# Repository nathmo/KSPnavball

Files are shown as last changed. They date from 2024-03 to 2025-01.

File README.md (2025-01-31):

# KSPnavball
This is a mechanical navball for a custom KSP gamepad



# Current state
currently it can be assembled but the wheel have nylon wheel and are too slippery. I'm experimenting with wheel made out of TPU but I need something even more rubbery and sticky. 
Regarding the software the main idea is here and the ball move but due to the slippage it's hard to tell if the code is doing it's job or if I fucked up the math to get the transform. (plus it definitely need some tunning)
anyways, feel free to build it and help me iron out the kink :)


# open issue
Ball slippage, omniwheel grip issue. I need to find a way to make the wheel more sticky and ruberry so that it works correctly.

# Hardware
|QTY|Name|Link|total price|
|---|----|----|----|
|25X|M3 5 mm depth 4.5mm diamater heat insert |https://www.aliexpress.com/item/1005003582355741.html|3.5$|
|25X|M3 screw | ||
|3X |omniwheel |https://www.aliexpress.com/item/32960657744.html| 8$|
|3X |DC motor |https://www.aliexpress.com/item/33022320164.html|  7$|
|2X |Hbridge DRV8833 |https://www.aliexpress.com/item/1005006444609771.html| 2.5$|
|1X |3 axis magnetometer ||  4.5$ |
|1X |magnet cylinder 10x2mm |https://www.aliexpress.com/item/1005006362930902.html| 2$ |
|1X |arduino nano |https://www.aliexpress.com/item/1005005702204423.html|2.5$|
Total = ~30 $ + 3D printed part + transparent window

one laser cutted sheet of 5mm transparent material is required. It should be engraved with the center sign of the navball.
the plastic part should not require any support and can be printed on a 15 x 15 [cm] bed
you will find the required file to print in the folder ToPrint, same for the folder toCut

# Wiring
need to document

# Software

https://kerbalsimpitrevamped-arduino.readthedocs.io/en/latest/payloadstructs.html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

https://kerbalsimpitrevamped-arduino.readthedocs.io/en/latest/payloadstructs.html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
https://www.instructables.com/KerbalController-a-Custom-Control-Panel-for-Rocket/

# Kinematic


The sphere is 90 mm in diameter
the wheel are 50 mm in diameter
the wheel are 120° apart (see from the top) and 45° raised from the horizontal plane

To compute the required motor commande $\alpha_1, \alpha_2, \alpha_3$ we need to break down the problem in two parts : 
1) finding the required rotation to go from the current navball orientation to the target one.
2) project this rotation on the wheels so that we know how much to rotate each motor.

### Find the required rotation
this is solved using [quaternion](https://en.wikipedia.org/wiki/Quaternion). We know two things :
1) the ball current orientation in the form of a unitary quaternion $(c_0, c_1, c_2, c_3)$ and
2) the target orientation in the form of a unitary quaternion $(t_0, t_1, t_2, t_3)$

from theses we know that there must exist a unitary quaternion such that $q \cdot c = t $ and thus we can deduce $q = tc^{-1}$
$c^{-1}$ being the conjugate of c, compute as $c^{-1}=(c_0, -c_1, -c_2, -c_3)$. unitary mean that the norm $c_0^2+c_1^2+c_2^2+c_3^2$ of the quaternion is equal to 1.
in practice this is compute like this :

$$
\begin{aligned}
q_0 &: c_0 t_0 + c_1 t_1 + c_2 t_2 + c_3 t_3, \\
q_1 &: -c_1 t_0 + c_0 t_1 - c_3 t_2 + c_2 t_3, \\
q_2 &: -c_2 t_0 + c_3 t_1 + c_0 t_2 - c_1 t_3, \\
q_3 &: -c_3 t_0 - c_2 t_1 + c_1 t_2 + c_0 t_3.
\end{aligned}
$$

$q_0$ represent the ammount of rotation and $q_1, q_2, q_3$ represent the rotation axis direction $(x,y,z)$

### project it on the motor axis
we use linear algebra to project the quaternion axis on the axis of each motor. then we scale this by the required rotation.

first we can precompute the vector basis on which we are going to project the rotation (3 vector that represent the rotation made by the three omniwheel)
we have our motor raised 45° from the horizontal plane. the unit axis for the first motor is thus :

$$
\text{First axis } (u_1): \text{Rotate vertical } (z) \ 45^\circ \text{ around } y:
u_1 = \begin{bmatrix}
\frac{\sqrt{2}}{2} \\
0 \\
\frac{\sqrt{2}}{2}
\end{bmatrix}.
$$

then we apply a $\pm 120°$ rotation around the z axis and obtain the two other vector.

$$
\text{Second axis } (u_2): \text{Rotate } u_1 \ +120^\circ \text{ around } z:
u_2 = \begin{bmatrix}
-\frac{\sqrt{2}}{4} \\
\frac{\sqrt{6}}{4} \\
\frac{\sqrt{2}}{2}
\end{bmatrix}.
$$

$$
\text{Third axis } (u_3): \text{Rotate } u_1 \ -120^\circ \text{ around } z:
u_3 = \begin{bmatrix}
-\frac{\sqrt{2}}{4} \\
-\frac{\sqrt{6}}{4} \\
\frac{\sqrt{2}}{2}
\end{bmatrix}.
$$

we know that there must be a vector $\alpha$ such that $\mathbf{M} \alpha = \mathbf{w}$, where $\alpha$ are the "ammount" projected on each wheel, $w$ is the rotation axis found previously using quaternion. $M$ is the matrix made from $\mathbf{M} = \begin{bmatrix} \mathbf{u}_1 & \mathbf{u}_2 & \mathbf{u}_3 \end{bmatrix}$

thus if we invert the matrix M we get :

$$M = \frac{1}{9} \begin{bmatrix}
10 & -2 & -2 \\
-2 & 10 & -2 \\
-2 & -2 & 10
\end{bmatrix}.$$

this matrix is computed once and stored in the code and the problem can now be easily solved using a matrix product $\alpha = \mathbf{M}^{-1}\mathbf{w}$

Now we convert the Quaternion to Rotation Vector to get w

Given $\mathbf{q} = (q_0, q_1, q_2, q_3)$,

Rotation angle: $\theta = 2 \arccos(q_0)$

Rotation axis (normalized): 
$$v = \frac{1}{\sqrt{1 - q_0^2}} \begin{bmatrix} q_1 \\ q_2 \\ q_3 \end{bmatrix}$$

Rotation vector: $w = \theta \mathbf{v}$

(we get w by encoding the ammoung of rotation into v the unitary axis vector.

# Calibration
we have a magnetometer and a magnet embeded in the sphere, how to calibrate and then deduce the sphere orientation from the magnetic field felt by the magnetometer ?

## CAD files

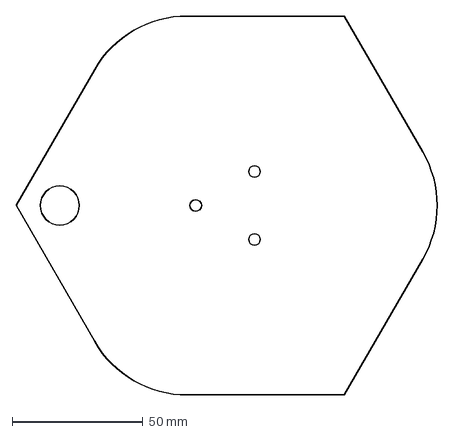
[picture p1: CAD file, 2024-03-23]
toCut/1XbackCover5mmWood.dxf
162.9 x 145.0 mm

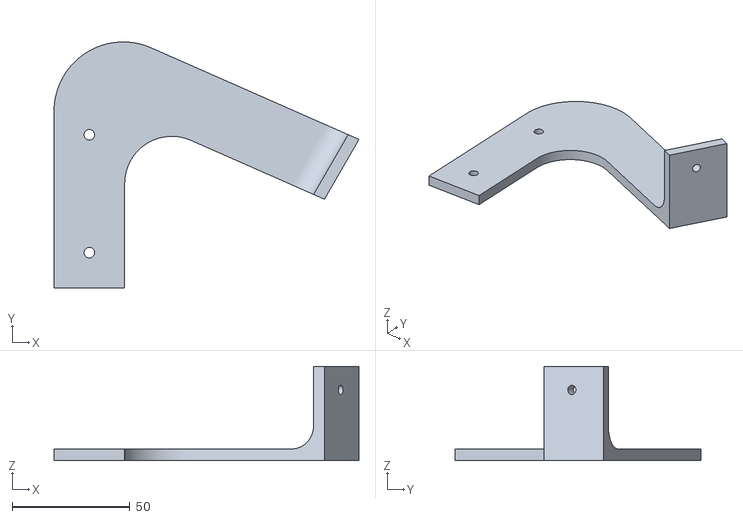
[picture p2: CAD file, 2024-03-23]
toPrint/1XBracketFixtureL.stl
129.4 x 104.4 x 40.0

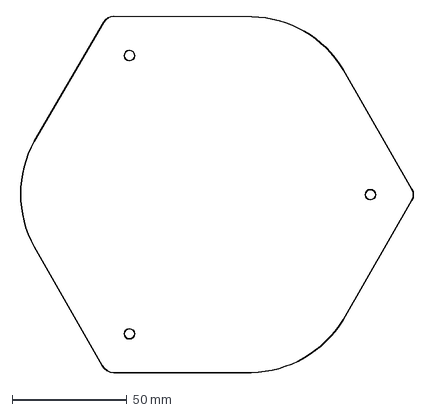
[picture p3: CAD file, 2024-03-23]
toCut/1XfrontCover5mmPlexi.dxf
173.3 x 155.2 mm

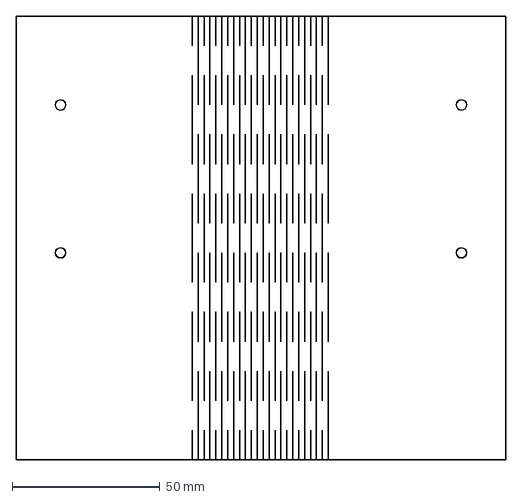
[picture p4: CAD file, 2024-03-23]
toCut/3XsideLivingHinge.dxf
165.5 x 150.0 mm

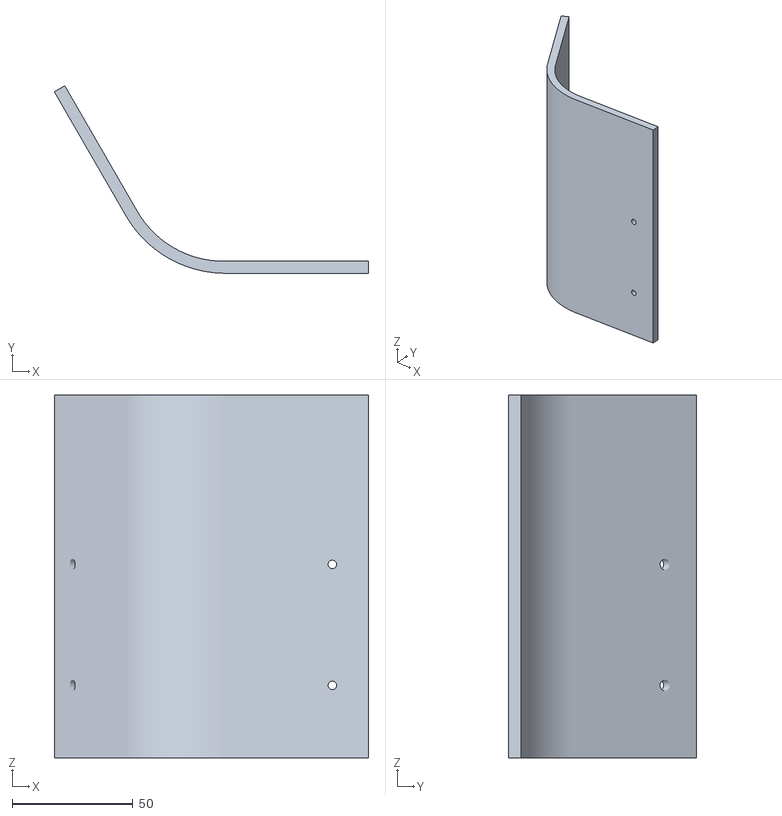
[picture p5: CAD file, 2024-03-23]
toPrint/3XSideCover.stl
129.9 x 77.5 x 150.0

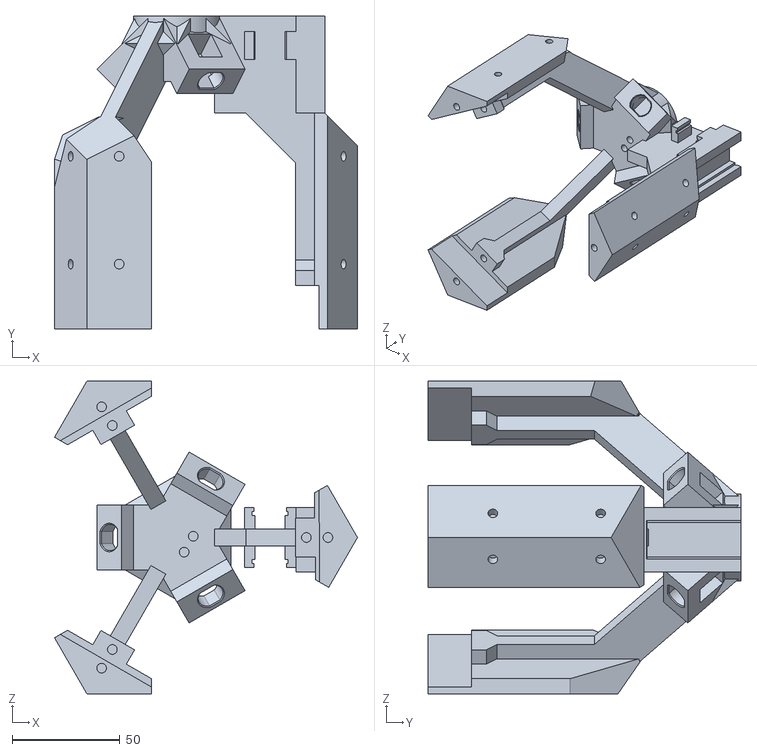
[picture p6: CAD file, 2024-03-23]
toPrint/1XmotorMOunt.stl
140.6 x 145.0 x 145.0

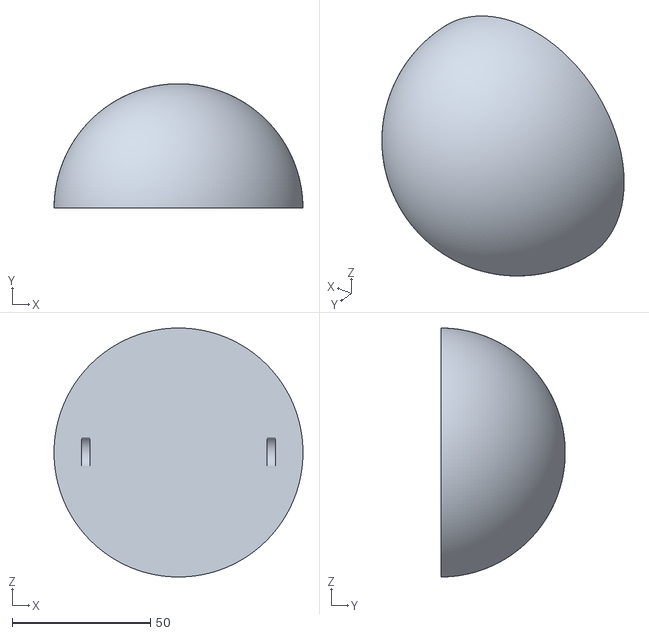
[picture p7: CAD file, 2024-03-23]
toPrint/2XhalfNavball.stl
90.0 x 45.0 x 90.0

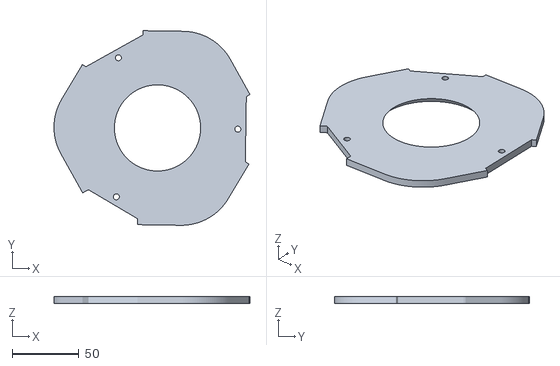
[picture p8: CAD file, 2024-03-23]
toPrint/1XNavballRetainer.stl
146.4 x 145.4 x 5.00

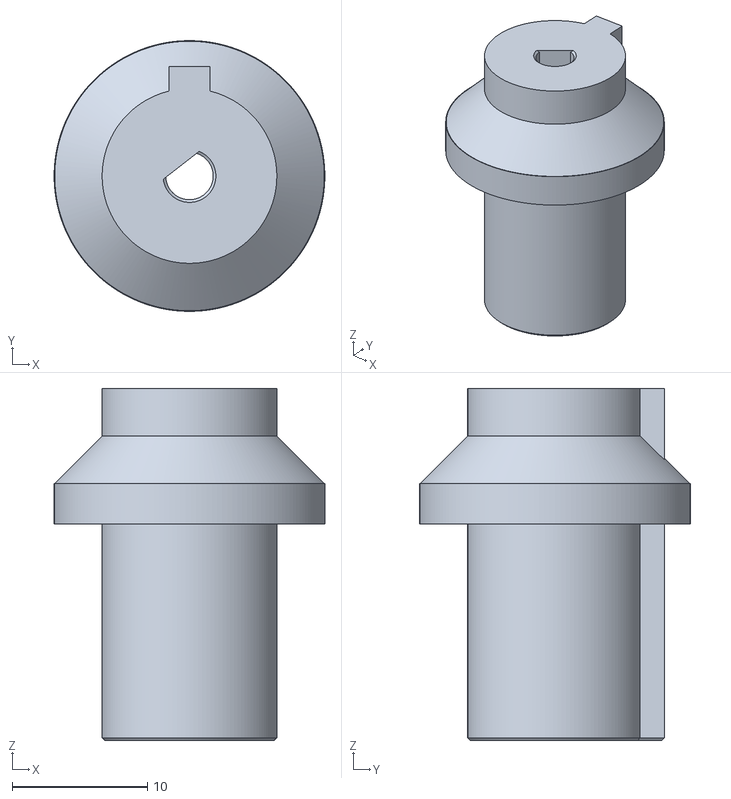
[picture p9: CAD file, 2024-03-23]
toPrint/3XCouplerWheelMotor.stl
20.0 x 20.0 x 26.0

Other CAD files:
toPrint/1XBracketFixtureR.stl

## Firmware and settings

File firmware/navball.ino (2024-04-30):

#include <Arduino.h>
#include <math.h>
#include "KerbalSimpit.h"

#define MOT_A1_PIN 6 // swap the order here if motor turn in reverse
#define MOT_A2_PIN 5
#define MOT_B1_PIN 10
#define MOT_B2_PIN 11
#define MOT_C1_PIN 3
#define MOT_C2_PIN 9

KerbalSimpit mySimpit(Serial);  // Declare a KerbalSimpit object that will communicate using the "Serial" device.

struct Quaternion {
    float w, x, y, z;
};

struct EulerAngles {
    float heading, pitch, roll;
};

Quaternion navballCurrentAttitude; // global variable with the current navball orientation
Quaternion shipAttitude; // global variable with the ship/goal orientation
int displayMODE=0; // select what to display on the navball (see the handler at the bottom)
float debugHeading;
float debugPitch;
float debugRoll;

float degreesToRadians(float degrees) {
    return degrees * (PI / 180.0);
}

// WARNING, USE RADIAN AND NOTE DEGREE !!!
Quaternion eulerToQuaternion(float heading, float pitch, float roll) {
    Quaternion q;

    float cy = cos(heading * 0.5);
    float sy = sin(heading * 0.5);
    float cp = cos(pitch * 0.5);
    float sp = sin(pitch * 0.5);
    float cr = cos(roll * 0.5);
    float sr = sin(roll * 0.5);

    q.w = cy * cp * cr + sy * sp * sr;
    q.x = cy * cp * sr - sy * sp * cr;
    q.y = sy * cp * sr + cy * sp * cr;
    q.z = sy * cp * cr - cy * sp * sr;

    return q;
}
//return degree !!!
EulerAngles quaternionToEulerAngles(Quaternion q) {
    EulerAngles angles;

    // Roll (x-axis rotation)
    float sinr_cosp = 2 * (q.w * q.x + q.y * q.z);
    float cosr_cosp = 1 - 2 * (q.x * q.x + q.y * q.y);
    angles.roll = atan2(sinr_cosp, cosr_cosp);

    // Pitch (y-axis rotation)
    float sinp = 2 * (q.w * q.y - q.z * q.x);
    if (fabs(sinp) >= 1)
        angles.pitch = copysign(M_PI / 2, sinp); // use 90 degrees if out of range
    else
        angles.pitch = asin(sinp);

    // Heading (z-axis rotation)
    float siny_cosp = 2 * (q.w * q.z + q.x * q.y);
    float cosy_cosp = 1 - 2 * (q.y * q.y + q.z * q.z);
    angles.heading = atan2(siny_cosp, cosy_cosp);

    // Convert radians to degrees
    angles.heading = angles.heading * 180.0 / M_PI;
    angles.pitch = angles.pitch * 180.0 / M_PI;
    angles.roll = angles.roll * 180.0 / M_PI;

    return angles;
}

void normalize(Quaternion& q) {
    float n = q.w*q.w+q.x*q.x+q.y*q.y+q.z*q.z;
    q.w /= n;
    q.x /= n;
    q.y /= n;
    q.z /= n;
}

Quaternion rotation_between_quaternions(const Quaternion& q1, const Quaternion& q2) {
    // Calculate the rotation needed between two quaternions q1 and q2
    Quaternion ret;
    ret.w = 1 + q1.x * q2.x + q1.y * q2.y + q1.z * q2.z;
    ret.x = q1.y * q2.z - q1.z * q2.y;
    ret.y = q1.z * q2.x - q1.x * q2.z;
    ret.z = q1.x * q2.y - q1.y * q2.x;
    normalize(ret);
    return ret;
}

// Function to project a quaternion as the sum of three static quaternions
// and return the coefficients for each quaternion
void projectQuaternion(Quaternion q, float &coeffA, float &coeffB, float &coeffC) {
    // Define the three static quaternions
    Quaternion A = {0.46193975, 0.1913417, 0.33141354456, 0.80010311354}; // roue A
    Quaternion B = {0.46193975, 0.1913417, -0.33141354456, -0.80010311354}; // roue B
    Quaternion C = {0.9238795, 0.3826834, 0, 0}; // roue C -> reflect the motor geomety 45° and 120°

    // Compute the projection coefficients
    float dotA = q.w * A.w + q.x * A.x + q.y * A.y + q.z * A.z;
    float dotB = q.w * B.w + q.x * B.x + q.y * B.y + q.z * B.z;
    float dotC = q.w * C.w + q.x * C.x + q.y * C.y + q.z * C.z;

    // Assign coefficients
    coeffA = dotA;
    coeffB = dotB;
    coeffC = dotC;
}

bool areQuaternionsClose(const Quaternion& q1, const Quaternion& q2, float threshold = 1e-6) {
    // Compute absolute difference between corresponding quaternion components
    float diffW = fabs(q1.w - q2.w);
    float diffX = fabs(q1.x - q2.x);
    float diffY = fabs(q1.y - q2.y);
    float diffZ = fabs(q1.z - q2.z);
    
    // Check if all differences are within the threshold
    return (diffW < threshold) && (diffX < threshold) && (diffY < threshold) && (diffZ < threshold);
}

void set_motor_pwm(int pwm, char motor)
{
  switch(motor) {
    case 'A':
      if (pwm < 0) {  // reverse speeds
        analogWrite(MOT_A1_PIN, -pwm);
        digitalWrite(MOT_A2_PIN, LOW);
      } else { // stop or forward
        digitalWrite(MOT_A1_PIN, LOW);
        analogWrite(MOT_A2_PIN, pwm);
      }
      break;
    case 'B':
      if (pwm < 0) {  // reverse speeds
        analogWrite(MOT_B1_PIN, -pwm);
        digitalWrite(MOT_B2_PIN, LOW);
      } else { // stop or forward
        digitalWrite(MOT_B1_PIN, LOW);
        analogWrite(MOT_B2_PIN, pwm);
      }
      break;
    case 'C':
      if (pwm < 0) {  // reverse speeds
        analogWrite(MOT_C1_PIN, -pwm);
        digitalWrite(MOT_C2_PIN, LOW);
      } else { // stop or forward
        digitalWrite(MOT_C1_PIN, LOW);
        analogWrite(MOT_C2_PIN, pwm);
      }
      break;
  }
}

void stop_all_motor()
{
  digitalWrite(MOT_A1_PIN, LOW);
  digitalWrite(MOT_A2_PIN, LOW);
  digitalWrite(MOT_B1_PIN, LOW);
  digitalWrite(MOT_B2_PIN, LOW);
  digitalWrite(MOT_C1_PIN, LOW);
  digitalWrite(MOT_C2_PIN, LOW);
}

void setup() {
    // Set all the motor control inputs to OUTPUT
  pinMode(MOT_A1_PIN, OUTPUT);
  pinMode(MOT_A2_PIN, OUTPUT);
  pinMode(MOT_B1_PIN, OUTPUT);
  pinMode(MOT_B2_PIN, OUTPUT);
  pinMode(MOT_C1_PIN, OUTPUT);
  pinMode(MOT_C2_PIN, OUTPUT);
  // Turn off motors - Initial state
  digitalWrite(MOT_A1_PIN, LOW);
  digitalWrite(MOT_A2_PIN, LOW);
  digitalWrite(MOT_B1_PIN, LOW);
  digitalWrite(MOT_B2_PIN, LOW);
  digitalWrite(MOT_C1_PIN, LOW);
  digitalWrite(MOT_C2_PIN, LOW);

  pinMode(LED_BUILTIN, OUTPUT);
  // Turn on the built-in to indicate the start of the handshake process
  digitalWrite(LED_BUILTIN, HIGH);

  Serial.begin(115200);
  // This loop continually attempts to handshake with the plugin.
  // It will keep retrying until it gets a successful handshake.
  while (!mySimpit.init()) {
    delay(100);
  }
  // Turn off the built-in LED to indicate handshaking is complete.
  digitalWrite(LED_BUILTIN, LOW);
  // Display a message on screen in KSP
  if (mySimpit.connectedToKSP2()) mySimpit.printToKSP(F("navball connected to KSP2"), PRINT_TO_SCREEN);
  else mySimpit.printToKSP(F("navball connected to KSP1"), PRINT_TO_SCREEN);
  
  mySimpit.inboundHandler(messageHandler);

  // | Vessel Movement/Position | TODO find what is really required
  mySimpit.registerChannel(ALTITUDE_MESSAGE);
  mySimpit.registerChannel(VELOCITY_MESSAGE);
  mySimpit.registerChannel(AIRSPEED_MESSAGE);
  mySimpit.registerChannel(APSIDES_MESSAGE);
  mySimpit.registerChannel(APSIDESTIME_MESSAGE);
  mySimpit.registerChannel(MANEUVER_MESSAGE);
  mySimpit.registerChannel(SAS_MODE_INFO_MESSAGE);
  mySimpit.registerChannel(ORBIT_MESSAGE);
  mySimpit.registerChannel(ROTATION_DATA_MESSAGE);
}

void loop() {
  mySimpit.update();
  float coeffA, coeffB, coeffC;
  //the global variable are update with from the message handler
  if(!areQuaternionsClose(shipAttitude,navballCurrentAttitude)){ // we only move the ball if there is a significant difference between the two value.
    // we compute the difference with the current navball attitude
    Quaternion toRotate = rotation_between_quaternions(shipAttitude, navballCurrentAttitude);
    // we project to get how much need to rotate each motor
    projectQuaternion(shipAttitude, coeffA, coeffB, coeffC);

    set_motor_pwm(coeffA*255, 'A');
    set_motor_pwm(coeffB*255, 'B');
    set_motor_pwm(coeffC*255, 'C');
    // wait a set amount of time and stop.
    delay(2000); // calibrate with motor speed so that it can do one full rotation (or find better scheme)
    stop_all_motor();
    navballCurrentAttitude = shipAttitude;
  }
  mySimpit.printToKSP("Heading: " + String(coeffA), PRINT_TO_SCREEN);
  mySimpit.printToKSP("Pitch: " + String(coeffB), PRINT_TO_SCREEN);
  mySimpit.printToKSP("Roll: " + String(coeffC), PRINT_TO_SCREEN);
  delay(1000);
}

void messageHandler(byte messageType, byte msg[], byte msgSize) {
  EulerAngles shipatitudeRADIAN;
  switch (messageType) {
    case ROTATION_DATA_MESSAGE: {
        if (msgSize == sizeof(vesselPointingMessage))
        {
          vesselPointingMessage vesselPointingMsg = parseMessage<vesselPointingMessage>(msg);
          if(displayMODE==0){
          shipatitudeRADIAN.heading = degreesToRadians(vesselPointingMsg.heading);
          shipatitudeRADIAN.pitch = degreesToRadians(vesselPointingMsg.pitch);
          shipatitudeRADIAN.roll = degreesToRadians(vesselPointingMsg.roll);
          shipAttitude = eulerToQuaternion(shipatitudeRADIAN.heading, shipatitudeRADIAN.pitch, shipatitudeRADIAN.roll);
          
          debugHeading = shipatitudeRADIAN.heading;
          debugPitch = shipatitudeRADIAN.pitch;
          debugRoll = shipatitudeRADIAN.roll;
          } else if (displayMODE==1){
          shipatitudeRADIAN.heading = degreesToRadians(vesselPointingMsg.orbitalVelocityHeading);
          shipatitudeRADIAN.pitch = degreesToRadians(vesselPointingMsg.orbitalVelocityPitch);
          shipatitudeRADIAN.roll = 0;
          shipAttitude = eulerToQuaternion(shipatitudeRADIAN.heading, shipatitudeRADIAN.pitch, shipatitudeRADIAN.roll);
          } else if (displayMODE==2){
          shipatitudeRADIAN.heading = degreesToRadians(vesselPointingMsg.surfaceVelocityHeading);
          shipatitudeRADIAN.pitch = degreesToRadians(vesselPointingMsg.surfaceVelocityPitch);
          shipatitudeRADIAN.roll = 0;
          shipAttitude = eulerToQuaternion(shipatitudeRADIAN.heading, shipatitudeRADIAN.pitch, shipatitudeRADIAN.roll);
          }
        }
      } break;
    case TARGETINFO_MESSAGE: {
        if (msgSize == sizeof(targetMessage)) 
        {
          targetMessage targetMsg = parseMessage<targetMessage>(msg);
          if(displayMODE==3){
          shipatitudeRADIAN.heading = degreesToRadians(targetMsg.heading);
          shipatitudeRADIAN.pitch = degreesToRadians(targetMsg.pitch);
          shipatitudeRADIAN.roll = 0;
          shipAttitude = eulerToQuaternion(shipatitudeRADIAN.heading, shipatitudeRADIAN.pitch, shipatitudeRADIAN.roll);
          } else if (displayMODE==4){
          shipatitudeRADIAN.heading = degreesToRadians(targetMsg.velocityHeading);
          shipatitudeRADIAN.pitch = degreesToRadians(targetMsg.velocityPitch);
          shipatitudeRADIAN.roll = 0;
          shipAttitude = eulerToQuaternion(shipatitudeRADIAN.heading, shipatitudeRADIAN.pitch, shipatitudeRADIAN.roll);
          }
        }
      } break;
    default: {
      } break;
  }
}

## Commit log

2024-01-23 added file to Print and cut
    [0XTransparentCover.stl, 1XBracket.stl, 1XBracketB.stl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]
2024-01-23 added the ball of the navball
    [1XNavball.stl]
2024-03-22 Update and rename Cover5mmPlexiAndWood.dxf to toCut/Cover5mmPlexiAndWood.dxf
    [Cover5mmPlexiAndWood.dxf]
2024-03-22 added kinematic
2024-03-22 updated kinematic
2024-03-23 Add files via upload
    clearance issue
    [3XCouplerWheelMotor.stl]
2024-03-23 added living hinge + small revision
    [1XbackCover5mmWood.dxf, 1XfrontCover5mmPlexi.dxf, 3XsideLivingHinge.dxf]
2024-04-30 not working but get data
    forgot to call the simpit refresh function... Now we get data but the motor dont seems to move yet :(
    [navball.ino]
